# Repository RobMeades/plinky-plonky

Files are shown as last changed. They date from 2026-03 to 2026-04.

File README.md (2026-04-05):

# Introduction
For Christmas 2025 Santa brought Hazel a music box mechanism, henceforth referred to as a "plinky-plonky".  Since it was difficult to turn at speed, I did a quick [motorised version](https://www.youtube.com/watch?v=XHdWuA18UNk) with some bits I was able to get hold of quickly: a motor controller with a speed knob on it and a 5&nbsp;V motor which purported to be silent.  The motor was not silent at all.

Since then I have made a [working Camberwick Green musical box](https://www.meades.org/misc/musical_box/musical_box.html) using one of these mechanisms, employing several varieties of stepper motor and a TMC2209 stepper motor controller.  Hence this repository describes how to make the updated version of the motorised plink-plonky, employing a much quieter stepper motor, TMC2209, ESP32 and using Bluetooth for control.

You can find a video of it in action on [YouTube](https://youtu.be/Unc9a-GsFBE); read on to find out what the lead weights are for.

In order to make this motorised plinky-plonky you will need to be able to:

- 3D print in FDM,
- solder,
- wire-up a small amount of electronics,
- write, or at least compile, C code (based on [ESP-IDF](https://docs.espressif.com/projects/esp-idf/en/stable/esp32/get-started/index.html) for the ESP32),
- write, or at least compile, an Android application to drive the Android Bluetooth API, or download and install the rather spiffy one from the [Releases](https://github.com/RobMeades/plinky-plonky/releases) section of this repo that Google Gemini wrote with a lot of prompting,
- do a tiny amount of woodwork (cutting circular shapes in plywood, sanding, glueing, varnishing).

You will need the following tools:

- an FDM 3D printer,
- a soldering iron,
- a wire stripper, 
- a wire snippers,
- a crimp tool for 0.1&nbsp;inch pitch connectors,
- a set of small allen keys, including 1.5&nbsp;mm and 2.5&nbsp;mm,
- an M3 tap and tap holder,
- a hair drier or other hot air blower capable of shrinking heat-shrink,
- a cross-head screwdriver,
- a largish magnetic flat-head screwdriver,
- an Android phone,
- a coping saw/jigsaw/clever-Dremel-thingy or other means of cutting circular shapes in thin plywood,
- a drill with 3&nbsp;mm and 10&nbsp;mm drill bits,
- fine grade sandpaper,
- a sanding block,
- optional: a very fine modellers paint brush.

# 3D Printed Parts
The 3D printed parts, along with exported `.stl`, are available in the [blender](/blender) folder; see there for printing instructions.

# Parts List
The following parts are required:

- the 3D printed parts from the [blender](blender) folder (which will require filament of your choice),
- a 15&nbsp;note plinky-plonky mechanism with fixing screws: the 3D printed parts are designed for one of [these](https://www.ebay.co.uk/itm/397247369927),
- an ESP32 board with headers soldered-in on the component side: the 3D printed parts are designed for one of [these](https://www.aliexpress.com/item/1005005780805655.html), you could of course modify them to take any small ESP32 board,
- a BigTreeTech TMC2209 board, i.e. one of [these](https://www.aliexpress.com/item/33028050145.html), any "sticky out" pins on the reverse lopped off and heatsink fitted,
- a 12/24&nbsp;V&nbsp;DC to 5&nbsp;V&nbsp;DC regulator: the 3D printed parts are designed for one of [these](https://www.aliexpress.com/item/1005010692851197.html), you could of course modify them to take any small regulator board; the current requirements for the 5&nbsp;V supply are negligible,
- a NEMA17 stepper motor: the 3D printed parts are designed for one of [these](https://www.amazon.co.uk/dp/B0D7PBB17L), frame size 42&nbsp;mm&nbsp;x&nbsp;42&nbsp;mm with M3 threaded mounting holes, frame 20&nbsp;mm deep, shaft 5&nbsp;mm diameter and 20&nbsp;mm long, with flat,
- an AC mains plug-top power supply capable of delivering up to 2&nbsp;Amps at between 12&nbsp;and&nbsp;24&nbsp;V&nbsp;DC, terminating in a 5.5&nbsp;mm diameter barrel connector with a 2.1&nbsp;mm diameter pin, centre-positive,
- an M3 hex-head grub screw (any length, the longer the better),
- 2 off M3&nbsp;x&nbsp;5&nbsp;mm hex head bolts,
- 3 off M3&nbsp;x&nbsp;10&nbsp;mm hex head bolts,
- 4 off M3&nbsp;x&nbsp;5&nbsp;mm pan head bolts,
- 3 off M3&nbsp;x&nbsp;10&nbsp;mm to 15&nbsp;mm pan head bolts,
- a panel-mount DC power socket with 2.1&nbsp;mm diameter pin, 5.5&nbsp;mm diameter barrel outer,
- 1 off 1&nbsp;kOhm resistor,
- a small amount of 7-strand wire in  a few shades of red/orange if you can (input DC Voltage, 5&nbsp;V and 3.3&nbsp;V), black and a signal colour of your choice (e.g. yellow or white or blue),
- a small amount (e.g. 100&nbsp;mm) of 3&nbsp;mm diameter heat-shrink,
- a small amount of flux-cored solder,
- 0.1&nbsp;inch pitch housings (1-way, 2-way and 4-way) plus female pins to go with,
- 2 off pieces (e.g. 10&nbsp;mm square) of double-sided sticky pad, tape or individual pads,
- a small amount (e.g. 400&nbsp;x&nbsp;250&nbsp;mm) of thin (e.g. 3&nbsp;mm thick) plywood,
- a small amount of wide (e.g. 30&nbsp;mm wide) edging that matches the plywood,
- optional: 1 off 4&nbsp;x&nbsp;8&nbsp;x&nbsp;3&nbsp;mm (inside diameter x outside diameter x thickness) bearing: I found that the sheath on the handle of the plinky-plonky mechanism rattled irritatingly so I took it off and slotted the handle into one of these bearings in the 3D printed wheel instead,
- PVA glue,
- possibly a little cyanoacrylate glue (AKA superglue),
- varnish or paint of your choice,
- a small amount of metallic paint (e.g. Humbrol&nbsp;11),
- optional: stick-on felt pads,
- optional: some 0.5&nbsp;kg lead weights e.g. [these from eBay](https://www.ebay.co.uk/itm/145559704455).

# Assembly Instructions
Assembly goes as follows (see also pictures below):

- if you intend to use the bearing to hold the handle of the plinky-plonky mechanism in the wheel, remove the sheath from the handle of the plinky-plonky mechanism by delving about in the end of it with a screwdriver to release the spring clip and hence the sheath,
- fix the plinky-plonky mechanism into place on top of the 3D printed body using the three fixing screws that were supplied with the mechanism, handle facing the stepper motor mount,
- fix the voltage regulator into place in the 3D printed body using the four M3&nbsp;x&nbsp;5&nbsp;mm pan head bolts, input end nearest the round hole in the side of the 3D printed body,
- I had trouble with resonance and, specifically the ESP32 and TMC2209 boards rattling very slightly, so I stuck a few pieces of sticky pad underneath where they would go to dampen things down a bit,
- clip the ESP32 and TMC2209 boards into their mounting positions in the 3D printed body, the TMC2209 board oriented with its red connector nearest the voltage regulator board, clipping the right hand side of both boards in first (when viewed with the lettering the right way up) in order to minimise the chances of damage; the USB-C connector of the ESP32 board needs to be lined up square with the rectangular hole in the 3D printed body,
- trim the stepper motor wires such that they will reach through the channel at the bottom left of the stepper motor mounting bracket and to the TMC22209 board mounting position in the 3D printed box (probably about 150&nbsp;mm) then terminate the wires in a 4-way 0.1&nbsp;inch pitch connector, order as in the schematic below, checking that the stepper motor you are using follows the same colour convention and adjusting as necessary,
- run an M3 tap through the grub screw hole in the 3D printed wheel,
- if you are using the 3D printed wheel that takes the 4&nbsp;x&nbsp;8&nbsp;x&nbsp;3&nbsp;mm bearing, fit the bearing int othe 3D printed wheel now,
- push the handle of the plinky-plonky mechanism into the offset hole in the 3D printed wheel then, with the grub screw hole and the flat on the stepper motor spindle uppermost, push the stepper motor spindle into the centre of the 3D printed wheel from the other side of its mounting bracket (i.e. so the spindle goes through the large central hole in the motor mounting bracket) and, as you do so, pass the stepper motor wires through the hole in the bottom left of the bracket and into the area of the 3D printed body where the boards will be mounted,
- fix the stepper motor to the mounting bracket with the two M3&nbsp;x&nbsp;5&nbsp;mm hex head bolts,
- screw the grub screw into the 3D printed wheel against the flat of the stepper motor spindle, making sure that there is a gap between the wheel and the stepper motor mounting bracket as you tighten the grub screw,
- using some 7-strand signal wire and heat-shrink as appropriate, make a short "Y" assembly with the 1&nbsp;kOhm resistor in series with one of the legs of the Y, all legs terminated in single 0.1&nbsp;inch pitch connectors (see picture below),
- using this, the remaining 7-strand wire and the 0.1&nbsp;inch pitch connectors, wire up the ESP32 board, the TMC2209 board and the stepper motor according to the schematic below, bringing 5&nbsp;V from the output of the voltage regulator and 12&nbsp;to&nbsp;24&nbsp;V from the input of the voltage regulator (you may chose different IO pins on the ESP32 board if you wish, these will be set later when the software for the ESP32 is compiled, though note that pin&nbsp;8 is not used since there is a blue LED on the board connected to this pin and pin&nbsp;20 is not used as it is internally connected to the RF inside the chip),
- wire the panel-mount power socket to the input of the voltage regulator board, with the central pin of the panel mount socket to the positive, adding heat-shrink to cover any exposed connector (since there is little room in the box),
- fit the panel-mount power socket into its mounting hole in the 3D printed body,
- plug an AC mains 12&nbsp;/nbsp;24&nbsp;V DC plug-top power supply into the power socket and you should see a red light on the ESP32 board,
- fix the 3D printed stepper motor cover to the stepper motor mounting bracket with two of the M3&nbsp;x&nbsp;10&nbsp;mm hex head bolts,
- fix the 3D printed lid into position over the electronics with the remaining M3&nbsp;x&nbsp;10&nbsp;mm hex head bolt,
- proceed to "Bring Up" below.

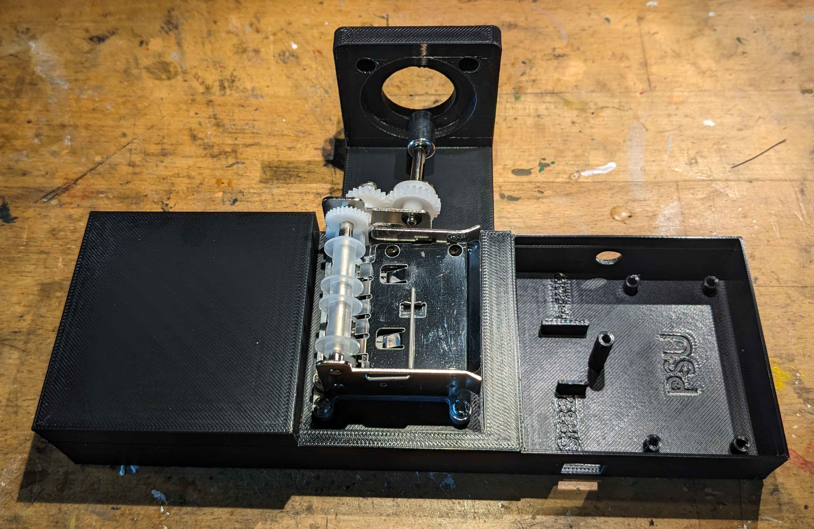
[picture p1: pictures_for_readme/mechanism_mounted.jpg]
Mechanism mounted
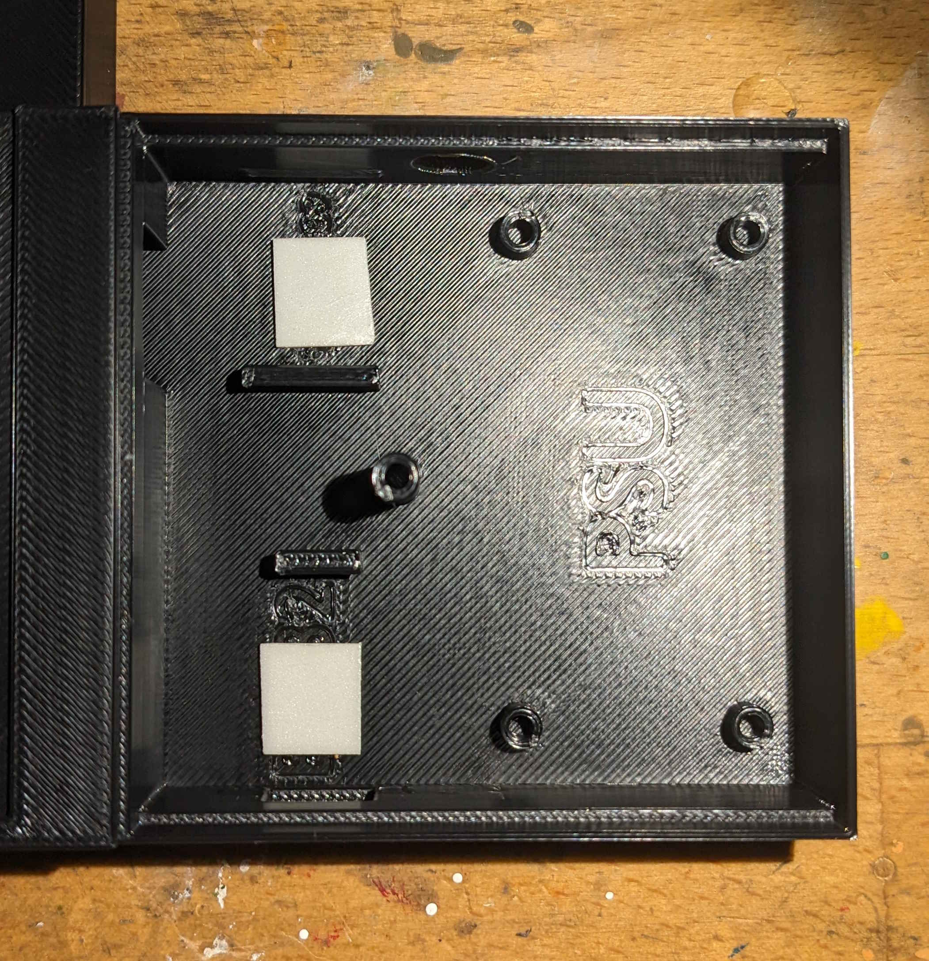
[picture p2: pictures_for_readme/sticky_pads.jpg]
Sticky pads
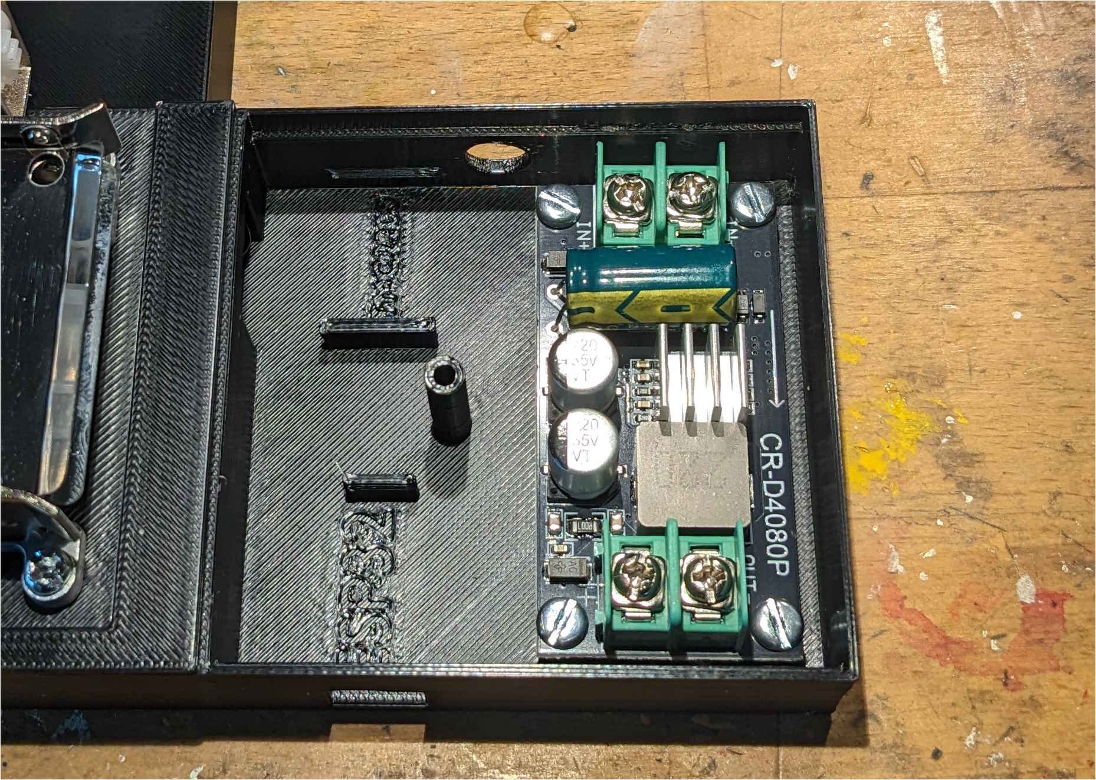
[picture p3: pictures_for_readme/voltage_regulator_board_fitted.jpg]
Voltage regulator board fitted
  

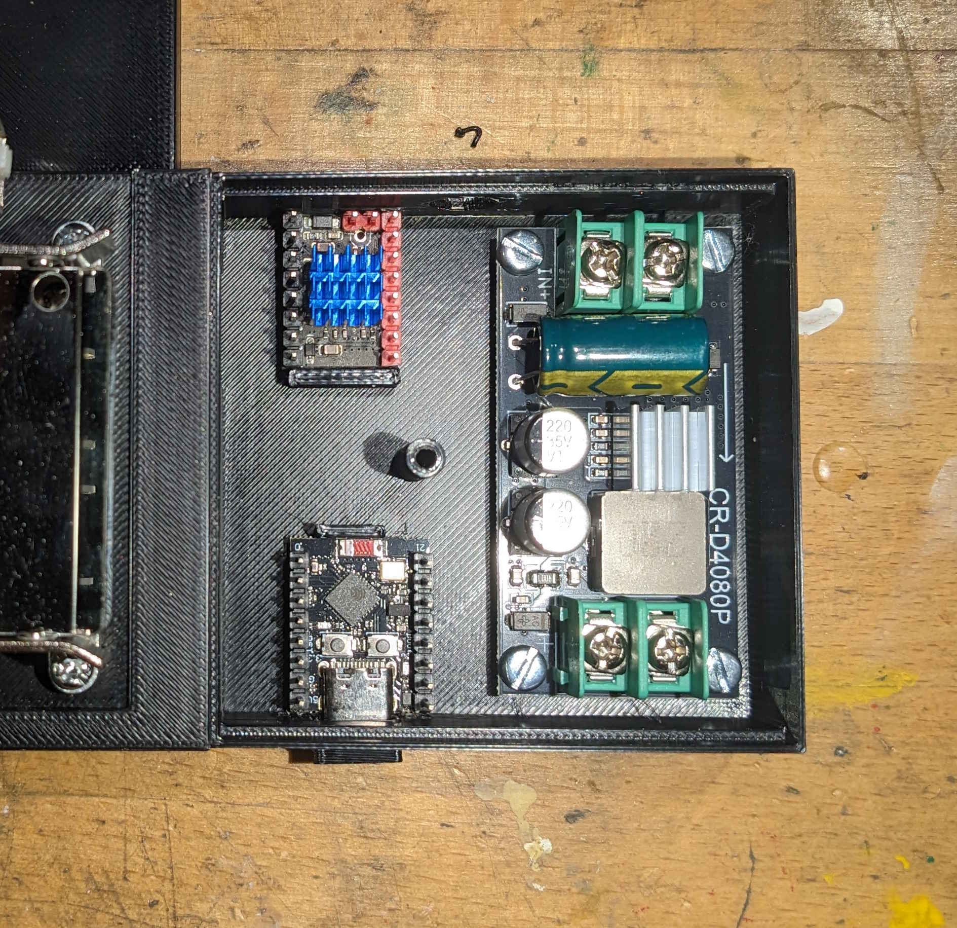
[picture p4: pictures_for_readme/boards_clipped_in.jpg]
Boards clipped in
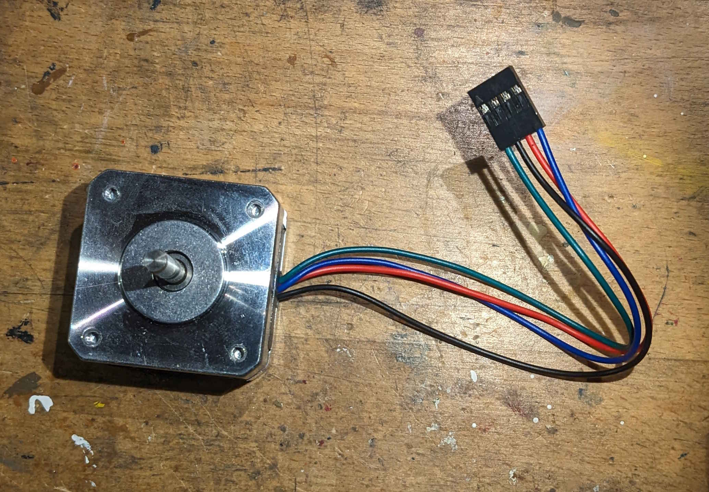
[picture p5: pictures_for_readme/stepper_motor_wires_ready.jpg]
Stepper motor wires trimmed and connector fitted
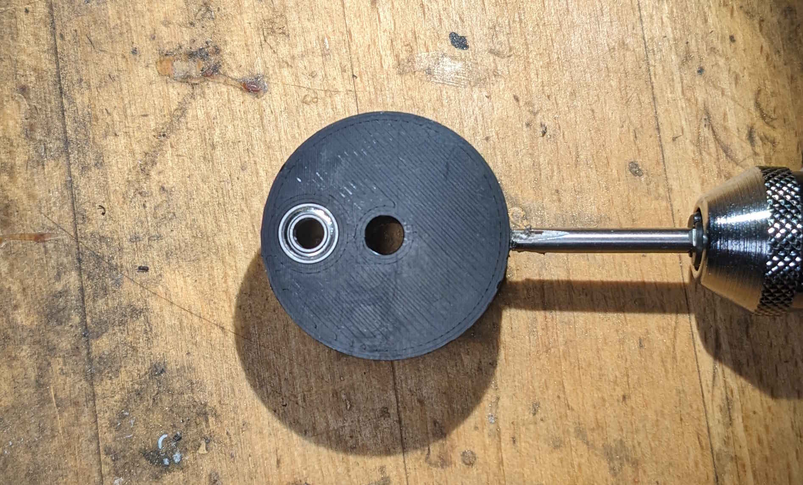
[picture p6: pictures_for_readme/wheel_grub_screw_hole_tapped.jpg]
Wheel grub screw hole tapped
  

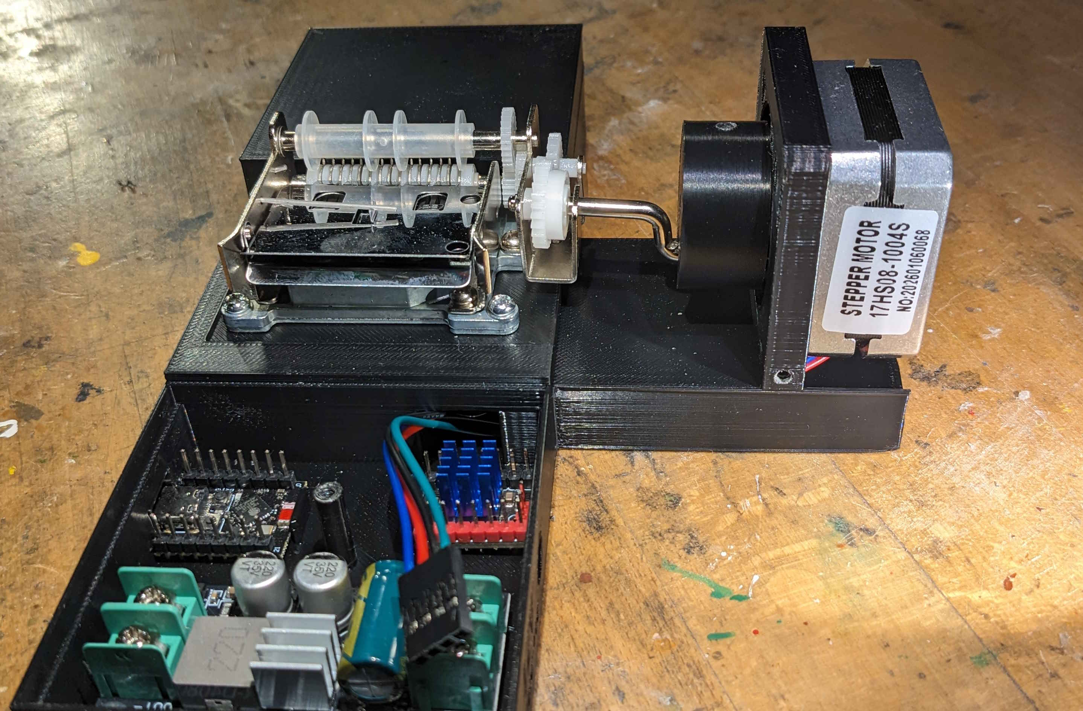
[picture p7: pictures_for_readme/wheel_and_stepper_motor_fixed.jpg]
Wheel and stepper motor fixed
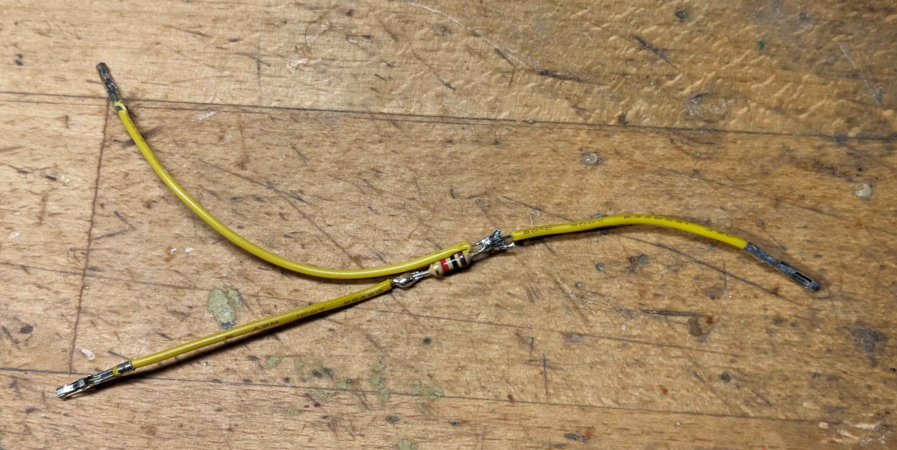
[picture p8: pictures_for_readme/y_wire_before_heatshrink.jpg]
Y-wire before heatshrink
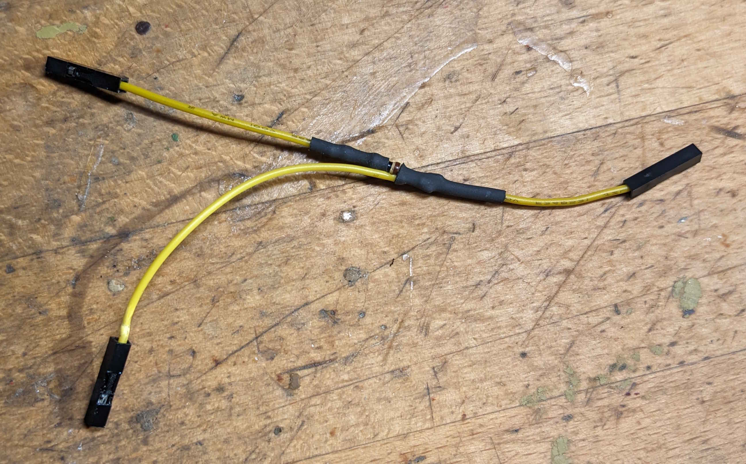
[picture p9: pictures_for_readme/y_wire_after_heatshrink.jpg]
Y-wire after heatshrink
  

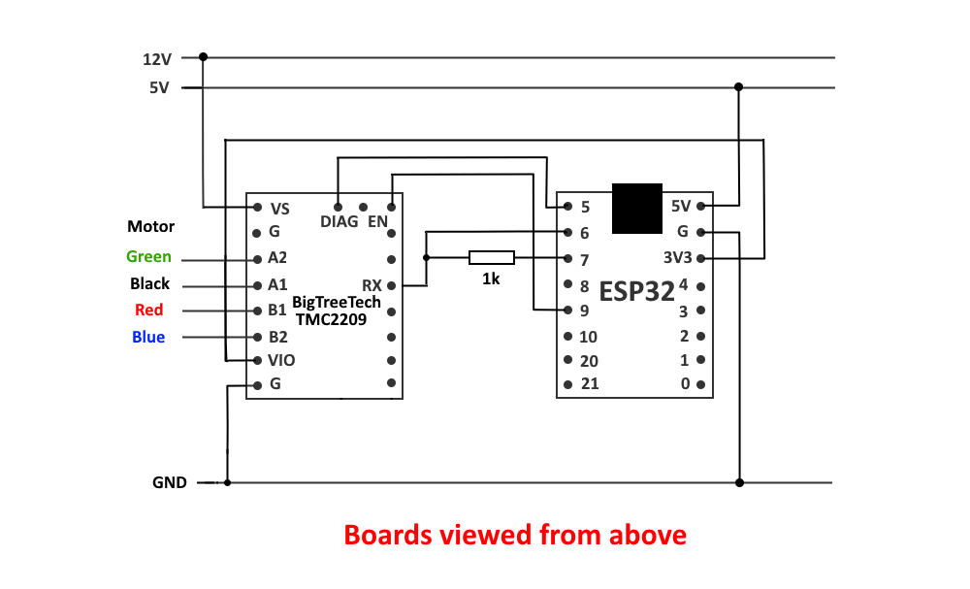
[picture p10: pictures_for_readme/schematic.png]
Schematic


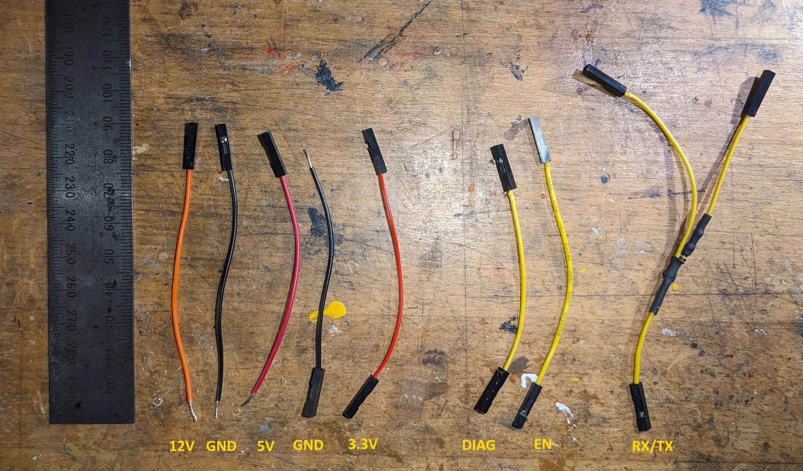
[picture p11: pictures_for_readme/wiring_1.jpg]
Wires cut to length and connectors fitted
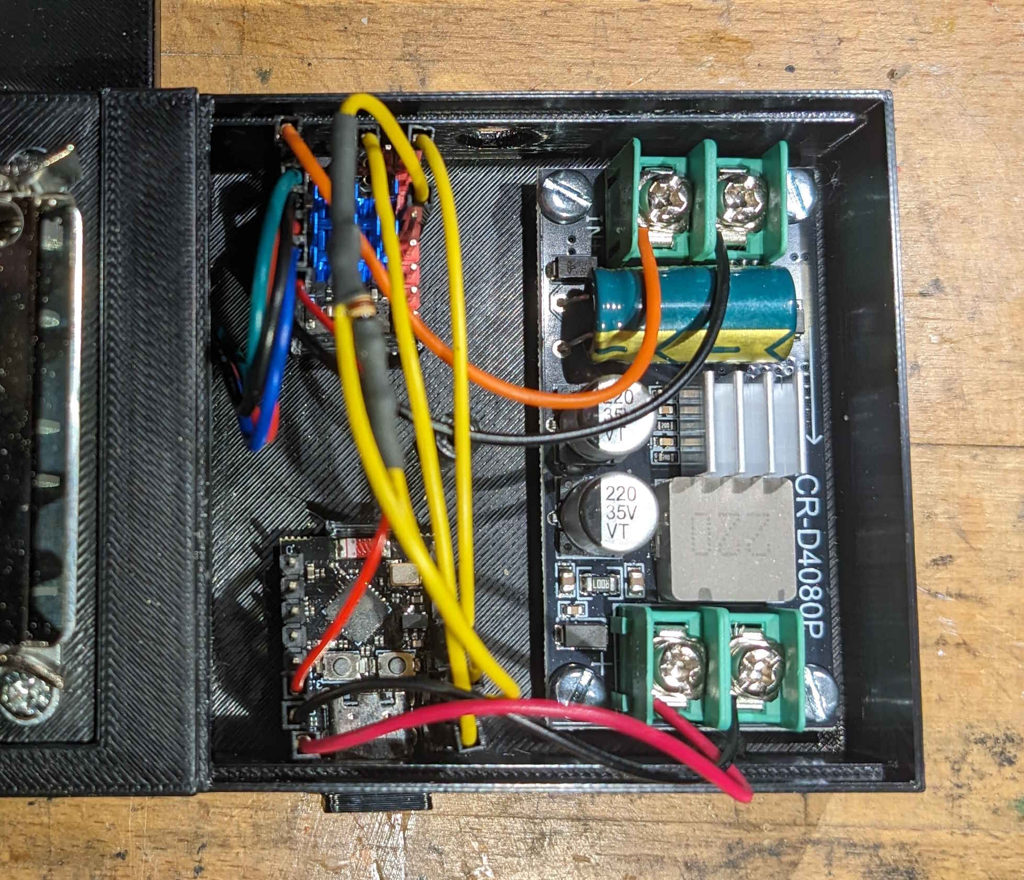
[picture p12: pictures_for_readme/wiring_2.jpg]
Wiring completed
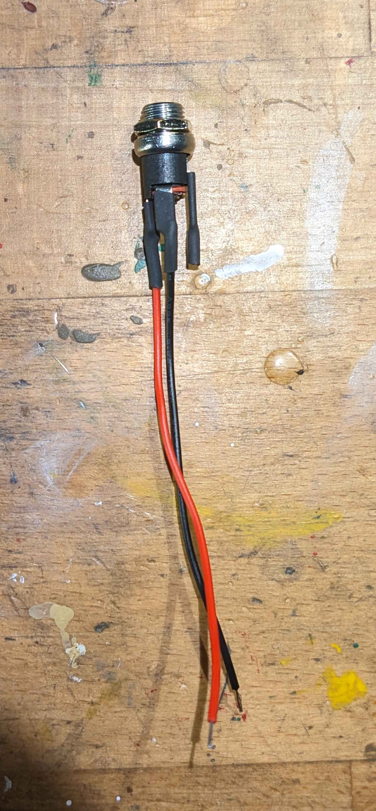
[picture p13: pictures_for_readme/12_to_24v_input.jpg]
power socket with wires attached and heat-shrinked
  

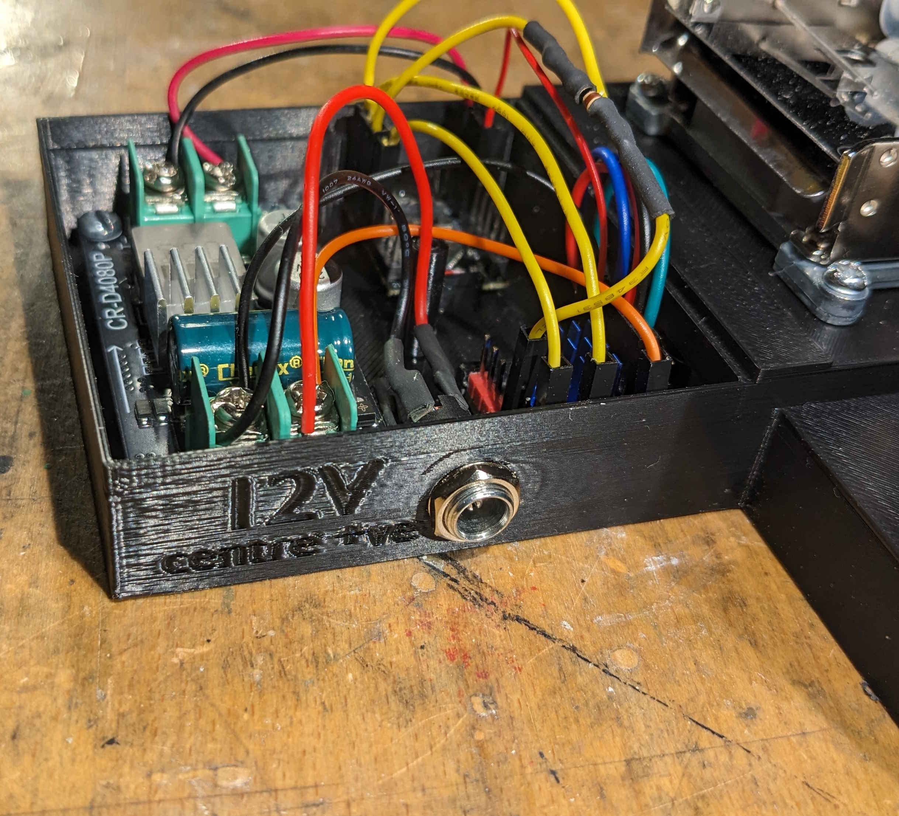
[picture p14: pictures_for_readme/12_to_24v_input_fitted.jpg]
power socket fitted
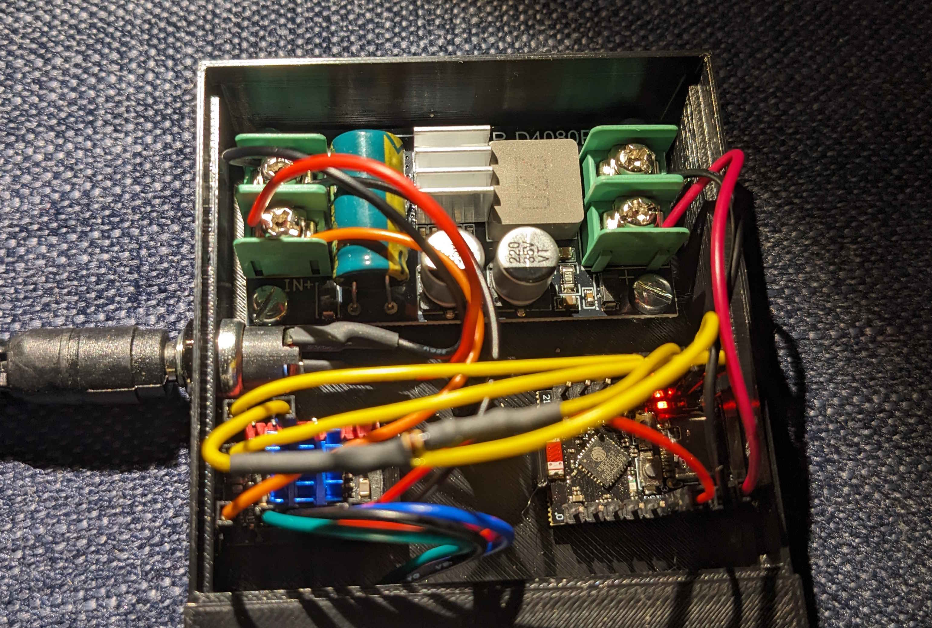
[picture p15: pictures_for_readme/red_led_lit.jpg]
power plugged in, LED lit
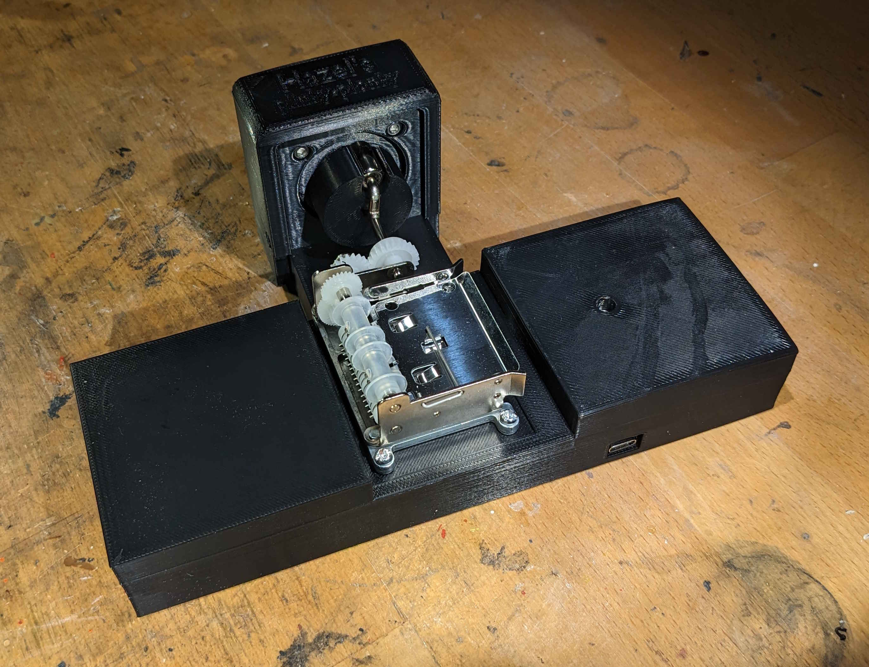
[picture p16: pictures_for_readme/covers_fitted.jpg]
Covers fitted
  

# Bring Up
Bring up goes as follows:

- plug a PC on which the [ESP-IDF software environment](https://docs.espressif.com/projects/esp-idf/en/stable/esp32/get-started/index.html) has been installed into the USB socket of the ESP32 board: a USB device should appear on the PC (e.g. `/dev/ttyACM0` on Linux); there is no need to plug external power into the plinky-plonky just yet as it should be able to draw sufficient power for these initial tests from the USB,
- build the software that is contained in the [software/esp32](/software/esp32) directory and download it to the ESP32 via USB; if you have wired up different GPIO pins on the ESP32 to those in the schematic above, change the values in [Kconfig.projbuild](/software/esp32/main/Kconfig.projbuild) before compiling,
- when the code runs on the ESP32 nothing much should happen, you will need an Android application for that, but if you see a splurge of "STALL" in the logged output of the ESP32 then you _do_ need to supply external power to the plinky-plonky,
- either install the pre-built Android `.apk` from the [Releases](https://github.com/RobMeades/plinky-plonky/releases) section of this repository on an Android phone or, if you wish to build/modify the application yourself, follow the instructions in the [software/android](/software/android) directory; Android will show a `Play Protect` warning, which is normal for an independent, open-source project: to install tap `More Details` and then `Install Anyway`,
- make sure you have Bluetooth enabled on the Android phone, hold the phone upright (portait orientation) and launch the application,
- give the application the permissions it asks for (required to access Bluetooth) and, with the plinky-plonky powered-up, use the application to scan for and connect to the plinky-plonky; if the Android phone fails to find the plinky-plonky, try disabling and then re-enabling Bluetooth on the phone and trying again (Android Bluetooth is a mess),
- press `Play` to have the motor run, `Stop` to stop it, adjust the speed using the knob or turn the phone landscape for the ability to generate complicated speed patterns,
- if you find that the plinky-plonky rattles at certain speeds, even when you have used the bearing approach, that will likely be because the handle can be slightly loose in the bearing: should that be the case, drop a _very_ tiny amount of cyanoacrylate glue between the handle and the inner face of the bearing to stop it rattling around, being _extremely_ careful not to get any glue on the runners of the bearing as you do so,
- rattles/resonance can also be removed by going around and gently tighting the fixing bolts,
- if that fails, since resonances can be in different components at different frequencies, I purchased some lead weights and kept three to hand for placing on whatever bit of the plinky-plonky needed damping at that running frequency (obviously wash your hands after handling lead),
- when you are satisfied that the plinky-plonky runs sweetly, push the 3D printed USB cover into the rectangular hole in the 3D printed body to prevent anything getting into the USB connector and proceed to "Finishing Off" below.

# Finishing Off
In order to give the plinky-plonky a solid yet resonant (in a good way) base:

- cut two pieces of thin plywood to the shape of the 3D printed `base_outer` (see pictures below),
- into one of these pieces drill three 3&nbsp;mm diameter holes to match the positions of the holes in the bottom of the 3D printed body, orienting that body nicely,
- into the other piece drill three rather wider (e.g. 10&nbsp;mm diameter) access holes in the same locations,
- glue the two pieces of plywood, in the same orientation, either side of `base_outer` with PVA, to make a kind of giant Oreo cookie, ensuring that the holes and the access holes align,
- glue an edging strip that matches the colour of the plywood around `base_outer` with PVA,
- when the glue has set, rub the whole thing down with fine sandpaper,
- varnish/finish in whatever way pleases you,
- to make the next step easier, create the threads in each of the holes in the bottom of the 3D printed body using one of the longer M3 pan head bolts,
- using the access holes to get at the 3&nbsp;mm diameter holes, attach the wooden/plastic base to the bottom of the 3D printed body with the longer M3 pan head bolts; a magnetic flat-head screwdriver is your friend,
- if you find that the plink-plonky resonates somewhat when running placed on a hard surface, stick-on felt pads or rubber feet help.

Finally, pick out the lettering embossed into the 3D printed stepper motor cover in metallic paint using a very fine modeller's paint brush.

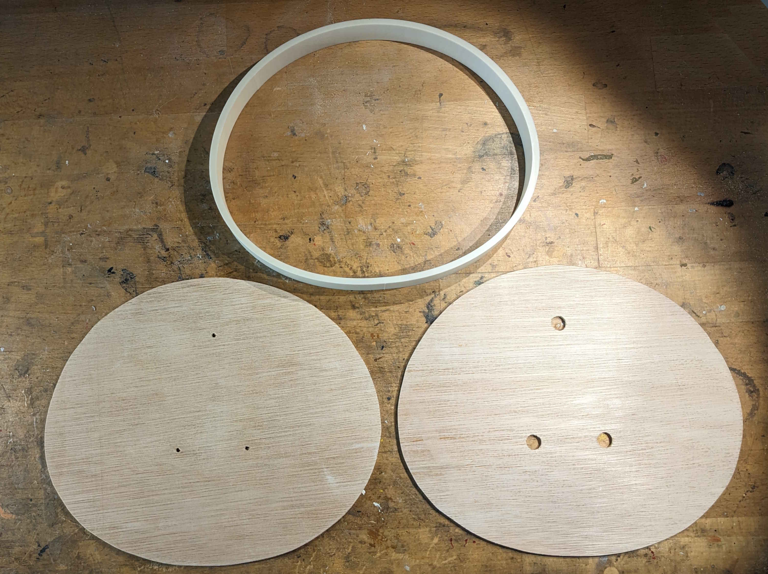
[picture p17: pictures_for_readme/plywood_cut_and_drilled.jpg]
Plywood cut and drilled
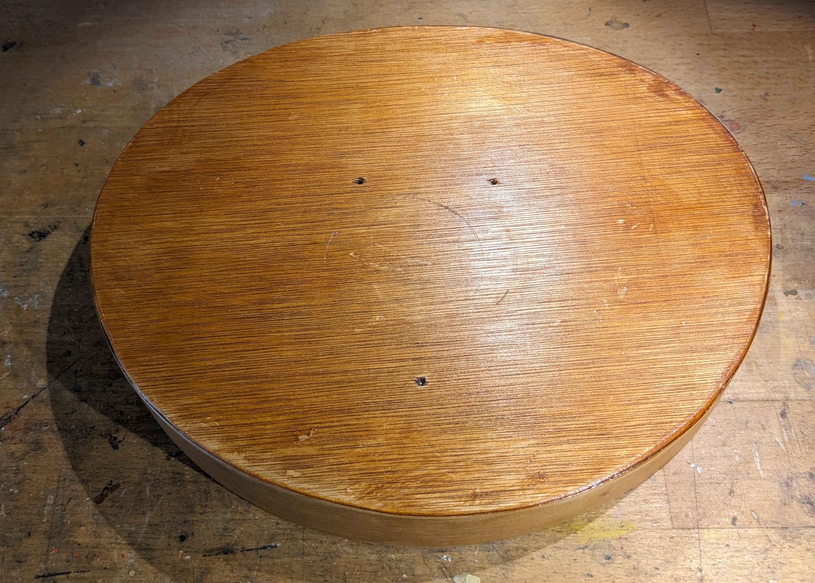
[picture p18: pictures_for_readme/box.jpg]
Box, varnished
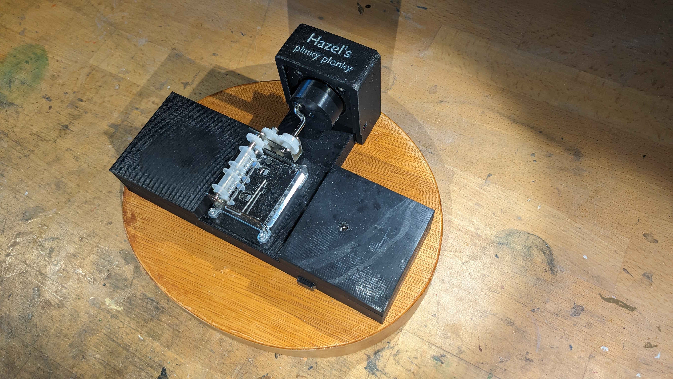
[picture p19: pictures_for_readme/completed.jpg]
Completed


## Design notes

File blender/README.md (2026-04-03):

# Introduction
This folder contains the 3D printed parts.  I printed all of the parts in ASA for longevity but any material will do.

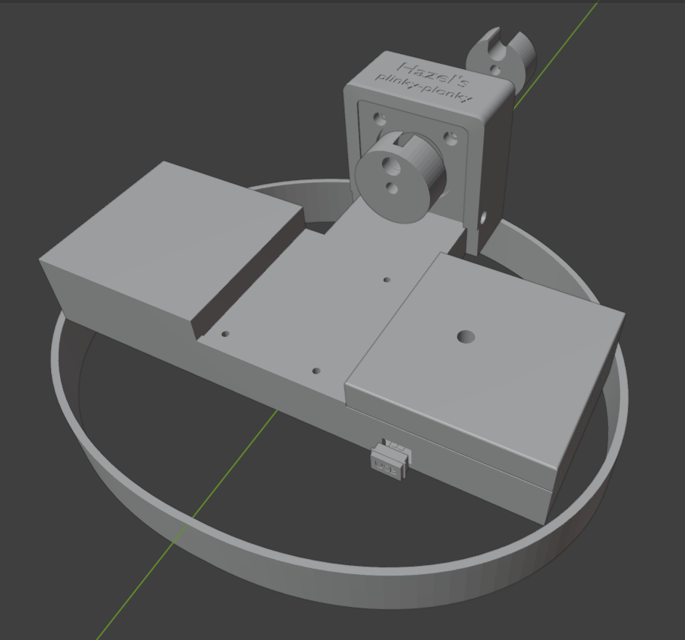
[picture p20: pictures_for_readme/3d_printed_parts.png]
Blender


# Printing Instructions
All parts should be printed at fastest speed, 15% in-fill, probably in black, aside from `base_outer` which you may wish to print in natural ASA, a better colour match for the plywood that it will be sandwiched between.  No supports should be required for any part except for the lid, which will need supports on the build plate for the screw hole.

You have a choice where the wheel is concerned: print either `wheel_for_unmodified_handle` or `wheel_for_handle_no_sheath`.  I found that the sheath on the handle of the plinky-plonky mechanism, designed to make operating it by hand easier, wrattled irritatingly and so I took the sheath off and printed `wheel_for_handle_no_sheath` into which I fitted a 4&nbsp;x&nbsp;8&nbsp;x&nbsp;3&nbsp;mm bearing to take the inner part of the handle.  If you prefer not to remove the sheath, print `wheel_for_unmodified_handle` instead.

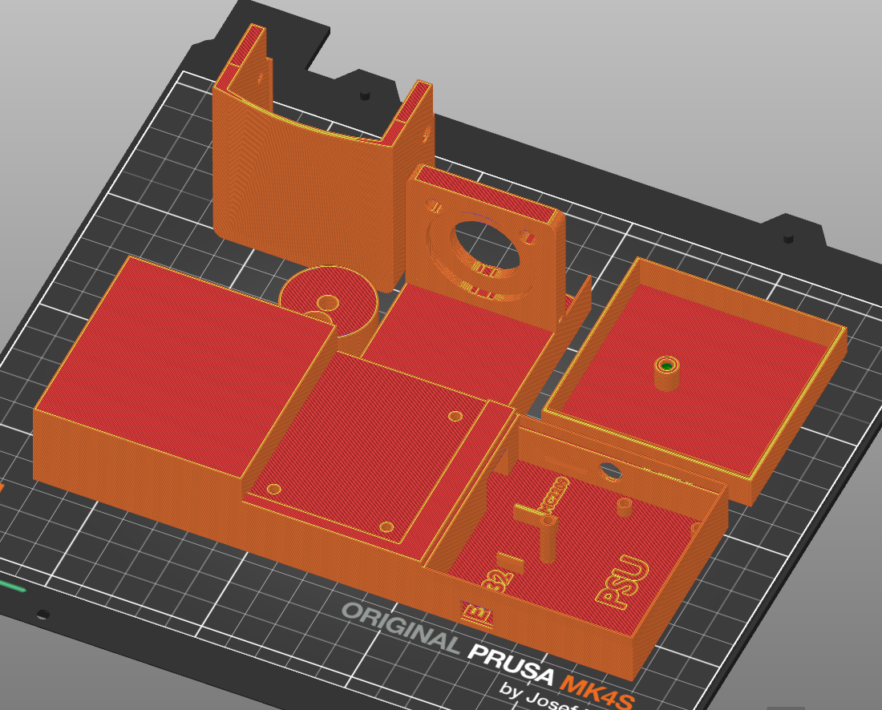
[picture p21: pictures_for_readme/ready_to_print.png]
Main parts ready to print
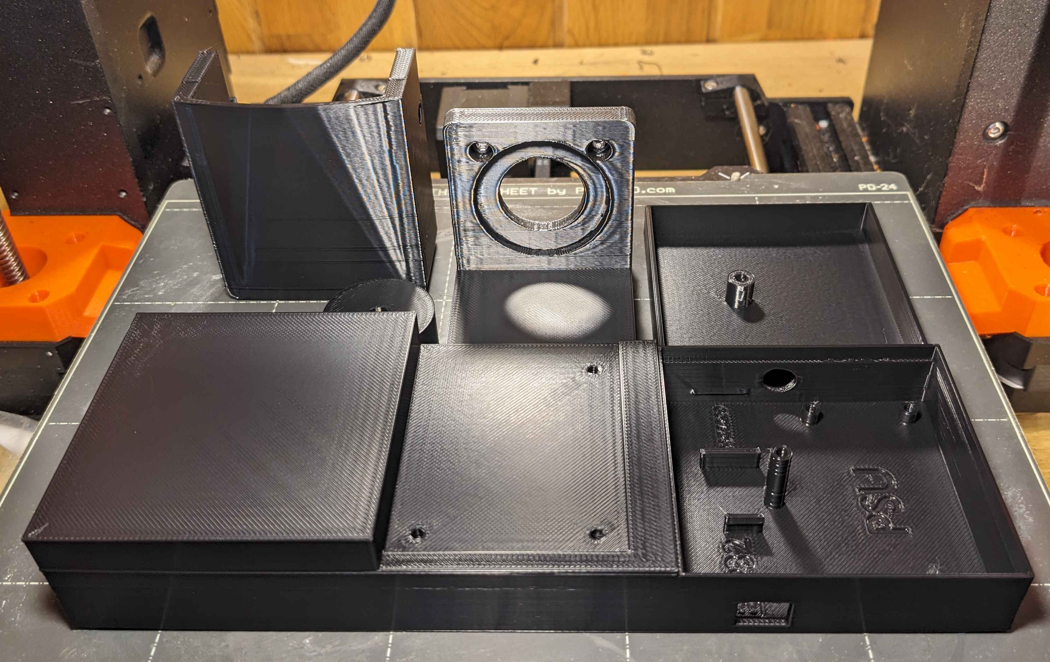
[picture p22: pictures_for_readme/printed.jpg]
Main parts printed
 

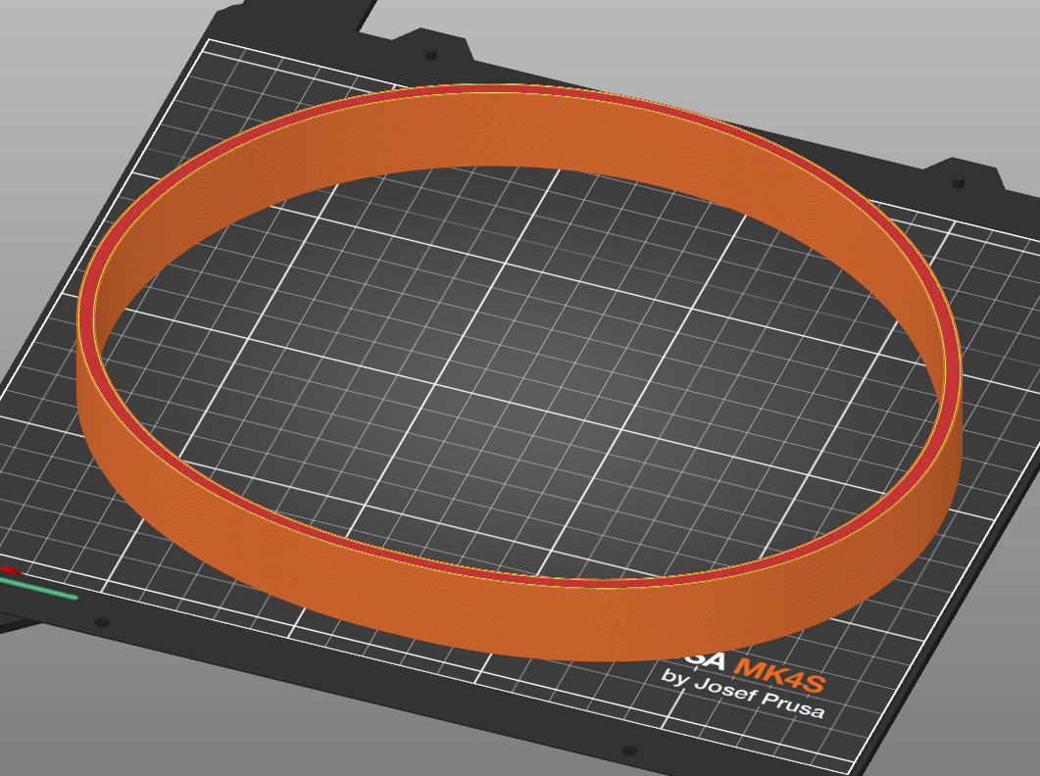
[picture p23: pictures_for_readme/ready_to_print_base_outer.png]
Base outer ready to print
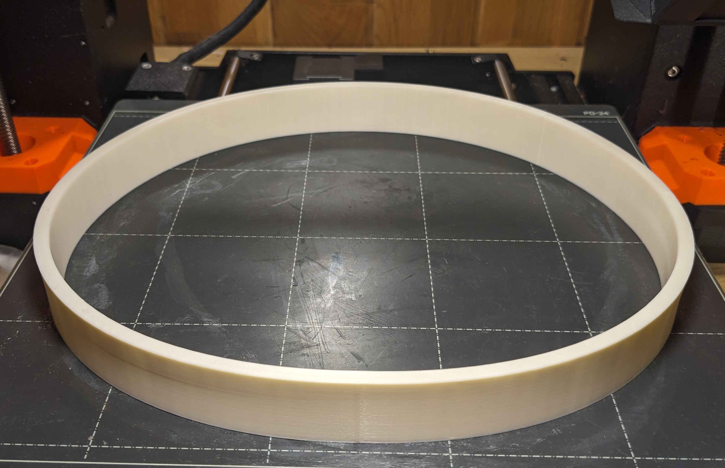
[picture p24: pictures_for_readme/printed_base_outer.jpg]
Base outer printed


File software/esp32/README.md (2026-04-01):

# Introduction
This folder contains the software for the ESP32-side of the plinky-plonky.

On a PC set up with the [ESP-IDF](https://docs.espressif.com/projects/esp-idf/en/stable/esp32/get-started/index.html) software environment, compile this software with the default values and download it to the ESP32 in the plinky-plonky using a USB cable.  If you have chosen to wire up different GPIO pins on the ESP32 to the ones given in the [schematic](/pictures_for_readme/schematic.png) on the main page, change those values in [Kconfig.projbuild](main/Kconfig.projbuild) before compiling.

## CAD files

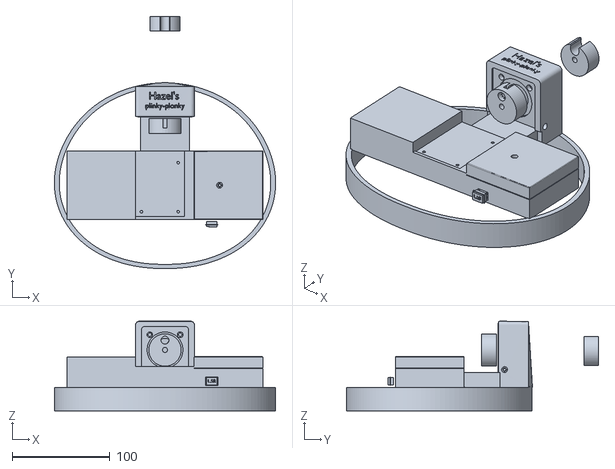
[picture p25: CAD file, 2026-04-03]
blender/plinky_plonky.stl
225.8 x 257.2 x 91.5

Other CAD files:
blender/plinky_plonky.blend

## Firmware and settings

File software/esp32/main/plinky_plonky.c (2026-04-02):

/*
 * Copyright 2026 Rob Meades
 *
 * Licensed under the Apache License, Version 2.0 (the "License");
 * you may not use this file except in compliance with the License.
 * You may obtain a copy of the License at
 *
 * http://www.apache.org/licenses/LICENSE-2.0
 *
 * Unless required by applicable law or agreed to in writing, software
 * distributed under the License is distributed on an "AS IS" BASIS,
 * WITHOUT WARRANTIES OR CONDITIONS OF ANY KIND, either express or implied.
 * See the License for the specific language governing permissions and
 * limitations under the License.
 */

/** @file
 * @brief Implementation of a steppper-motor driven plinky-plonky.
 */

#include <string.h>
#include <inttypes.h>
#include "freertos/FreeRTOS.h"
#include "freertos/task.h"
#include "freertos/queue.h"
#include "esp_event.h"
#include "esp_log.h"
#include "errno.h"
#include "driver/uart.h"
#include "driver/gpio.h"
#include "esp_timer.h"
#include "esp_task_wdt.h"
#include "nvs.h"
#include "nvs_flash.h"
#include "esp_bt.h"
#include "nimble/nimble_port.h"
#include "nimble/nimble_port_freertos.h"
#include "host/ble_hs.h"
#include "services/gap/ble_svc_gap.h"
#include "services/gatt/ble_svc_gatt.h"
#include "host/ble_gap.h"
#include "host/ble_hs.h"
#include "host/ble_store.h"
#include "host/ble_sm.h"      // For security manager constants
#include "host/util/util.h"

#include "tmc2209.h"

/* ----------------------------------------------------------------
 * COMPILE-TIME MACROS
 * -------------------------------------------------------------- */

 // Logging prefix
 #define TAG "plinky-plonky"

// UART buffer
#define UART_RX_BUFFFER_SIZE 256

// The addresss of the TMC2209 device we are going to us
#define TMC2209_ADDRESS 0

// The number of milliseconds to vTaskDelay() for in order to let the idle task
// to feed its watchdog
 #define WATCHDOG_FEED_TIME_MS 10

// The sense resisitor wired to the BRA and BRB pins of the TMC2209,
// the BigTreeTech board uses 100 milliOhms
#define TMC2209_RSENSE_MOHM 110

// Standard short duration for an LED lash
#define DEBUG_LED_SHORT_MS 50

// Standard short duration for a long LED lash
#define DEBUG_LED_LONG_MS 1000

// The motor current to set, in milliAmps
#define STEPPER_MOTOR_ACTIVE_CURRENT_MA 1000

// The percentage of the run current to apply during hold;
// don't need a lot, let it cool down
#define STEPPER_MOTOR_HOLD_CURRENT_PERCENT 20

// The microstep resolution to employ
#define STEPPER_MOTOR_MICROSTEP_RESOLUTION 256

// The default stepper motor velocity
#define STEPPER_MOTOR_DEFAULT_VELOCITY_MILLIHERTZ (64 * 7 * STEPPER_MOTOR_MICROSTEP_RESOLUTION)

// The maximum speed change step to do it one go
#define STEPPER_MOTOR_SPEED_MILLIHERTZ_CHANGE_MAX 1000000

// The speed change step when starting
#define STEPPER_MOTOR_SPEED_MILLIHERTZ_START_MAX 10

// The interval between speed changes if they have to
// be done in more than one step
#define STEPPER_MOTOR_SPEED_MILLIHERTZ_CHANGE_INTERVAL_MS 0

// The name that we appear under in Bluetooth
#define BLE_DEVICE_NAME "Plinky-Plonky"

// Service UUID for plinky-plonky control
#define PLINKY_PLONKY_SERVICE_UUID            0xFFE0

// Characteristic UUID for "play" command (Boolean)
#define PLINKY_PLONKY_PLAY_UUID               0xFFE1

// Characteristic UUID for "speed" command (uint32_t)
#define PLINKY_PLONKY_SPEED_MILLIHERTZ_UUID   0xFFE2

// The name for the speed entry in non-volatile storage.
#define NVS_NAME_SPEED "speed"

/* ----------------------------------------------------------------
 * TYPES
 * -------------------------------------------------------------- */

// The context for the plinky-plonky.
typedef struct {
    TaskHandle_t stall_task_handle;
    SemaphoreHandle_t diag_semaphore;
    QueueHandle_t ble_command_queue;
    TaskHandle_t ble_command_task_handle;
    ble_uuid16_t plinky_plonky_service_uuid;
    struct ble_hs_adv_fields ble_adv_fields;
    uint16_t ble_connection_handle;
    bool running;
    bool play_not_stop;
    uint32_t speed_milliHertz;
} plinky_plonky_context_t;

// Plinky-plonky commands.
typedef enum {
    COMMAND_NONE,
    COMMAND_UNKNOWN,
    COMMAND_WRITE_PLAY,
    COMMAND_WRITE_SPEED_MILLIHERTZ,
    COMMAND_READ_PLAY,
    COMMAND_READ_SPEED_MILLIHERTZ
} command_type_t;

// Command queue contents.
typedef struct {
    uint16_t uuid;
    command_type_t type;
    uint32_t value;
} command_t;

/* ----------------------------------------------------------------
 * VARIABLES (THERE ARE MORE FURTHER DOWN)
 * -------------------------------------------------------------- */

// Set up valid advertising parameters.
static const struct ble_gap_adv_params g_ble_adv_params = {
    .conn_mode = BLE_GAP_CONN_MODE_UND,   // Connectable undirected advertising
    .disc_mode = BLE_GAP_DISC_MODE_GEN,   // General discoverable mode
    // Values are in 0.625ms units
    // 160 = 100ms, 320 = 200ms
    .itvl_min = 160,                      // Minimum advertising interval (100 ms)
    .itvl_max = 320};                     // Maximum advertising interval (200 ms)

// Context for the whole application
static plinky_plonky_context_t g_plinky_plonky_context = {
    .stall_task_handle = NULL,
    .diag_semaphore = NULL,
    .ble_command_queue = NULL,
    .ble_command_task_handle = NULL,
    .plinky_plonky_service_uuid = BLE_UUID16_INIT(PLINKY_PLONKY_SERVICE_UUID),
    .ble_adv_fields = {0},
    .ble_connection_handle = BLE_HS_CONN_HANDLE_NONE,
    .running = true,
    .play_not_stop = false,
    .speed_milliHertz = STEPPER_MOTOR_DEFAULT_VELOCITY_MILLIHERTZ};

// THERE ARE MORE VARIABLE FURTHER DOWN

/* ----------------------------------------------------------------
 * STATIC FUNCTIONS: MISC
 * -------------------------------------------------------------- */

// Flash the debug LED
static void flash_debug_led(int32_t duration_ms)
{
#if defined(CONFIG_PLINKY_PLONKY_DEBUG_LED_PIN) && (CONFIG_PLINKY_PLONKY_DEBUG_LED_PIN >= 0)
    gpio_set_level(CONFIG_PLINKY_PLONKY_DEBUG_LED_PIN, 0);
    vTaskDelay(pdMS_TO_TICKS(duration_ms));
    gpio_set_level(CONFIG_PLINKY_PLONKY_DEBUG_LED_PIN, 1);
#endif
}

/* ----------------------------------------------------------------
 * STATIC FUNCTIONS: NVS RELATED
 * -------------------------------------------------------------- */

// Retrieve the stored speed value from NVS, returns
// ESP_ERR_NVS_NOT_FOUND if the value is not initialised.
static esp_err_t nvs_speed_millihertz_get(uint32_t *speed_milliHertz)
{
    nvs_handle_t nvs_handle;

    esp_err_t err = nvs_open("storage", NVS_READONLY, &nvs_handle);
    if (err == ESP_OK) {
        err = nvs_get_u32(nvs_handle, NVS_NAME_SPEED,
                          speed_milliHertz);
        if (err != ESP_OK) {
            ESP_LOGW(TAG, "Unable read \"%s\" from NVS:"
                     " 0x%04x (\"%s\")!", NVS_NAME_SPEED,
                      err, esp_err_to_name(err));
        }
        nvs_close(nvs_handle);
    } else {
        ESP_LOGE(TAG, "Unable to open NVS for read: 0x%04x (\"%s\")!", err, esp_err_to_name(err));
    }

    return err;
}

// Set the stored speed value in NVS.
static esp_err_t nvs_speed_millihertz_set(uint32_t speed_milliHertz)
{
    nvs_handle_t nvs_handle;

    esp_err_t err = nvs_open("storage", NVS_READWRITE, &nvs_handle);
    if (err == ESP_OK) {
        err = nvs_set_u32(nvs_handle, NVS_NAME_SPEED,
                          speed_milliHertz);
        if (err == ESP_OK) {
            err = nvs_commit(nvs_handle);
            if (err != ESP_OK)  {
                ESP_LOGE(TAG, "Unable to commit changes to NVS:"
                        " 0x%04x (\"%s\")!", err, esp_err_to_name(err));
            }
        } else {
            ESP_LOGE(TAG, "Unable write \"%s\" to NVS:"
                     " 0x%04x (\"%s\")!", NVS_NAME_SPEED,
                     err, esp_err_to_name(err));
        }
        nvs_close(nvs_handle);
    } else {
        ESP_LOGE(TAG, "Unable to open NVS for read/write: 0x%04x (\"%s\")!",
                 err, esp_err_to_name(err));
    }

    return err;
}

/* ----------------------------------------------------------------
 * STATIC FUNCTIONS: STEPPER MOTOR RELATED
 * -------------------------------------------------------------- */

#if defined CONFIG_PLINKY_PLONKY_DIAG_PIN && (CONFIG_PLINKY_PLONKY_DIAG_PIN >= 0)

// DIAG interrupt handler,
static void diag_interrupt_handler(void *handler_arg)
{
    plinky_plonky_context_t *context = (plinky_plonky_context_t *) handler_arg;
    BaseType_t higherPriorityTaskWoken;

    if (context->stall_task_handle && context->diag_semaphore) {
        xSemaphoreGiveFromISR(context->diag_semaphore, &higherPriorityTaskWoken);
        portYIELD_FROM_ISR(higherPriorityTaskWoken);
    }
}

#endif

// Task to handle stall indications.
static void stall_task(void *arg)
{
    plinky_plonky_context_t * context = (plinky_plonky_context_t *) arg;

    while (context->running) {
        xSemaphoreTake(context->diag_semaphore, portMAX_DELAY);
        ESP_LOGI(TAG, "STALL");
    }

    vTaskDelete(NULL);
}

/* ----------------------------------------------------------------
 * STATIC FUNCTION PROTOTYPE: NEEDED FOR BLE CALLBACKS
 * -------------------------------------------------------------- */

static int ble_gap_event_callback(struct ble_gap_event *event, void *arg);

/* ----------------------------------------------------------------
 * STATIC FUNCTIONS: BLE
 * -------------------------------------------------------------- */

// Change speed gradually.
static int32_t velocity_change(int32_t target_speed_millihertz)
{
    int32_t err = 0;
    int32_t target_velocity = target_speed_millihertz * STEPPER_MOTOR_MICROSTEP_RESOLUTION;
    int32_t velocity_step = STEPPER_MOTOR_SPEED_MILLIHERTZ_CHANGE_MAX * STEPPER_MOTOR_MICROSTEP_RESOLUTION;

    int32_t velocity = 0;
    tmc2209_get_velocity(TMC2209_ADDRESS, &velocity);
    if (target_velocity < velocity) {
        velocity_step = -velocity_step;
    }
    while ((velocity != target_velocity) && (err >= 0)) {
        velocity += velocity_step;
        if (velocity_step > 0) {
            if (velocity > target_velocity) {
                velocity = target_velocity;
            }
        } else {
            if (velocity < target_velocity) {
                velocity = target_velocity;
            }
        }
        err = tmc2209_set_velocity(TMC2209_ADDRESS, velocity);
        ESP_LOGI(TAG, "BLE tmc2209_set_velocity for velocity %d returned %d.", velocity, err);
        if ((err >= 0) && (velocity != target_velocity)) {
            vTaskDelay(pdMS_TO_TICKS(STEPPER_MOTOR_SPEED_MILLIHERTZ_CHANGE_INTERVAL_MS));
        }
    }

    return err;
}

// Task to handle BLE commands.
static void ble_command_task(void *arg)
{
    plinky_plonky_context_t * context = (plinky_plonky_context_t *) arg;
    command_t command;
    int32_t err = 0;
    int32_t velocity = 0;

    while (context->running) {
        if (xQueueReceive(context->ble_command_queue, &command, pdMS_TO_TICKS(100))) {
            switch (command.type) {
                case COMMAND_WRITE_PLAY:
                    context->play_not_stop = command.value;
                    // When stopping and starting we also change
                    // the velocity (gradually in the case of starting
                    // up), otherwise the motor can make a bit of a "clunk"
                    // noise
                    if (context->play_not_stop) {
                        tmc2209_motor_enable(TMC2209_ADDRESS);
                        err = velocity_change(context->speed_milliHertz);
                        if (err < 0) {
                            velocity = 0;
                            tmc2209_get_velocity(TMC2209_ADDRESS, &velocity);
                            ESP_LOGE(TAG, "BLE unable to set speed to %lu milliHertz at start (%d), speed"
                                    " is now %d milliHertz!", context->speed_milliHertz, err,
                                    velocity / STEPPER_MOTOR_MICROSTEP_RESOLUTION);
                            context->speed_milliHertz = velocity / STEPPER_MOTOR_MICROSTEP_RESOLUTION;
                        }
                    } else {
                        tmc2209_motor_disable(TMC2209_ADDRESS);
                        tmc2209_set_velocity(TMC2209_ADDRESS, 0);
                    }
                    ESP_LOGI(TAG, "BLE command (0x%04x), write: %s.",
                             command.uuid, context->play_not_stop ? "play" : "stop");
                    break;
                case COMMAND_WRITE_SPEED_MILLIHERTZ:
                    err = velocity_change((int32_t) command.value);
                    velocity = 0;
                    tmc2209_get_velocity(TMC2209_ADDRESS, &velocity);
                    context->speed_milliHertz = velocity / STEPPER_MOTOR_MICROSTEP_RESOLUTION;
                    if (err >= 0) {
                        ESP_LOGI(TAG, "BLE speed set to %lu milliHertz.", context->speed_milliHertz);
                        nvs_speed_millihertz_set(context->speed_milliHertz);
                    } else {
                        velocity = 0;
                        tmc2209_get_velocity(TMC2209_ADDRESS, &velocity);
                        ESP_LOGE(TAG, "BLE unable to set to %lu milliHertz (%d), speed"
                                 " is now %d milliHertz!", context->speed_milliHertz, err);
                    }
                    ESP_LOGI(TAG, "BLE command (0x%04x), write: speed %lu milliHertz.",
                             command.uuid, context->speed_milliHertz);
                    break;
                case COMMAND_READ_PLAY:
                    ESP_LOGI(TAG, "BLE command (0x%04x), read: %s.",
                             command.uuid, context->play_not_stop ? "play" : "stop");
                    break;
                case COMMAND_READ_SPEED_MILLIHERTZ:
                    ESP_LOGI(TAG, "BLE command (0x%04x), read: speed %lu milliHertz.",
                             command.uuid, context->speed_milliHertz);
                    break;
                case COMMAND_UNKNOWN:
                    ESP_LOGI(TAG, "BLE command (0x%04x) received unknown operation: %d (0x08x).",
                             command.uuid, command.value, command.value);
                    break;
                case COMMAND_NONE:
                default:
                    break;
             }
        }
        vTaskDelay(pdMS_TO_TICKS(WATCHDOG_FEED_TIME_MS));
    }

    vTaskDelete(NULL);
}

// Read up to four bytes from an mbuf, returning a
// int32_t made from them (with no endian changes,
// so the source must be litte-endian to work correctly).
static uint32_t mbuf_read(const struct os_mbuf *om)
{
    uint32_t value = 0;

    uint16_t len = os_mbuf_len(om);
    uint16_t read_len = sizeof(value);
    if (read_len > len) {
        read_len = len;
    }
    os_mbuf_copydata(om, 0, read_len, &value);
    ESP_LOGI(TAG, "BLE got data buffer length %d byte(s), extracting value %d.",
             len, value);

    return value;
}

// Play/Stop callback
static int plinky_plonky_play_callback(uint16_t conn_handle, uint16_t attr_handle,
                                       struct ble_gatt_access_ctxt *ctxt, void *arg)
{
    plinky_plonky_context_t *context = (plinky_plonky_context_t *) arg;
    int return_code = BLE_ATT_ERR_UNLIKELY;

    switch (ctxt->op) {
        case BLE_GATT_ACCESS_OP_WRITE_CHR:
        {
            // Read the  value
            uint32_t value = mbuf_read(ctxt->om);
            // Queue the command (non-blocking)
            command_t command = {.uuid = PLINKY_PLONKY_PLAY_UUID,
                                 .type = COMMAND_WRITE_PLAY,
                                 .value = value};
            xQueueSendFromISR(context->ble_command_queue, &command, NULL);
            // Send empty success response
            os_mbuf_free_chain(ctxt->om);
            ctxt->om = ble_hs_mbuf_from_flat("", 0);
            return_code = 0;
        }
            break;
        case BLE_GATT_ACCESS_OP_READ_CHR:
        {
            // Queue the command (non-blocking), purely for information
            command_t command = {.uuid = PLINKY_PLONKY_PLAY_UUID,
                                 .type = COMMAND_READ_PLAY,
                                 .value = 0};
            xQueueSendFromISR(context->ble_command_queue, &command, NULL);

            // Send the current setting
            os_mbuf_append(ctxt->om, &context->play_not_stop, sizeof(context->play_not_stop));
            return_code = 0;
        }
            break;
        default:
        {
            // Queue the command (non-blocking), for information
            command_t command = {.uuid = PLINKY_PLONKY_PLAY_UUID,
                                 .type = COMMAND_UNKNOWN,
                                 .value = ctxt->op};
            xQueueSendFromISR(context->ble_command_queue, &command, NULL);
        }
            break;
    }

    return return_code;
}

// Speed callback.
static int plinky_plonky_speed_callback(uint16_t conn_handle, uint16_t attr_handle,
                                        struct ble_gatt_access_ctxt *ctxt, void *arg)
{
    plinky_plonky_context_t *context = (plinky_plonky_context_t *) arg;
    int return_code = BLE_ATT_ERR_UNLIKELY;

    switch (ctxt->op) {
        case BLE_GATT_ACCESS_OP_WRITE_CHR:
        {
            // Read the value
            uint32_t value = mbuf_read(ctxt->om);
            // Queue the command (non-blocking)
            command_t command = {.uuid = PLINKY_PLONKY_SPEED_MILLIHERTZ_UUID,
                                 .type = COMMAND_WRITE_SPEED_MILLIHERTZ,
                                 .value = value};
            xQueueSendFromISR(context->ble_command_queue, &command, NULL);

            // Send empty success response
            os_mbuf_free_chain(ctxt->om);
            ctxt->om = ble_hs_mbuf_from_flat("", 0);
            return_code = 0;
        }
            break;
        case BLE_GATT_ACCESS_OP_READ_CHR:
        {
            // Queue the command (non-blocking), purely for information
            command_t command = {.uuid = PLINKY_PLONKY_SPEED_MILLIHERTZ_UUID,
                                 .type = COMMAND_READ_SPEED_MILLIHERTZ,
                                 .value = 0};
            xQueueSendFromISR(context->ble_command_queue, &command, NULL);

            // Send the current speed value
            uint32_t speed = context->speed_milliHertz;
            os_mbuf_append(ctxt->om, &speed, sizeof(speed));
            return_code = 0;
        }
            break;
        default:
        {
            // Queue the command (non-blocking), for information
            command_t command = {.uuid = PLINKY_PLONKY_SPEED_MILLIHERTZ_UUID,
                                 .type = COMMAND_UNKNOWN,
                                 .value = ctxt->op};
            xQueueSendFromISR(context->ble_command_queue, &command, NULL);
        }
            break;
    }

    return return_code;
}
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
void app_main(void)
{
    plinky_plonky_context_t *context = &g_plinky_plonky_context;

    ESP_LOGI(TAG, "Plinky-plonky app_main start");

    esp_err_t err = init(context);
    if (err == ESP_OK) {
        ESP_LOGI(TAG, "Initialization complete.");

        err = tmc2209_start(TMC2209_ADDRESS, CONFIG_PLINKY_PLONKY_ENABLE_PIN);

        if (err == ESP_OK) {
            ESP_LOGI(TAG, "Setting TMC2209 %d to %d.", TMC2209_ADDRESS,
                     STEPPER_MOTOR_MICROSTEP_RESOLUTION);
            err = tmc2209_set_microstep_resolution(TMC2209_ADDRESS,
                                                   STEPPER_MOTOR_MICROSTEP_RESOLUTION);
            if (err >= 0) {
                ESP_LOGI(TAG, "Microstep resolution is now %d.", err);
                err = ESP_OK;
            }
        }

#if defined CONFIG_PLINKY_PLONKY_DIAG_PIN && (CONFIG_PLINKY_PLONKY_DIAG_PIN >= 0)
        if (err == ESP_OK) {
            tmc2209_set_stallguard(TMC2209_ADDRESS, -1, 0);
        }
#endif

        // Allow us to feed the watchdog
        esp_task_wdt_add(NULL);

        if (err == ESP_OK) {
            ESP_LOGI(TAG, "Setting motor current to %d mA.", STEPPER_MOTOR_ACTIVE_CURRENT_MA);
            err = tmc2209_set_current(TMC2209_ADDRESS, TMC2209_RSENSE_MOHM,
                                      STEPPER_MOTOR_ACTIVE_CURRENT_MA,
                                      STEPPER_MOTOR_HOLD_CURRENT_PERCENT);
            if (err >= 0) {
                ESP_LOGI(TAG, "Current set to %d mA.", err);
                err = ESP_OK;
            }
        }

        if (err == ESP_OK) {
            ESP_LOGI(TAG, "Forcing StealthChop mode to stay on for quietness.");
            err = tmc2209_set_stealth_chop_threshold(TMC2209_ADDRESS, 0);
            if (err < 0) {
                ESP_LOGI(TAG, "Unable to force StealthChop mode on: %d!", err);
            }
        }

        if (err == ESP_OK) {
            ESP_LOGI(TAG, "Waiting for BLE connections/commands.");
            while (context->running) {
                // Let BLE commands do their thing
                vTaskDelay(pdMS_TO_TICKS(1000));
                esp_task_wdt_reset();
            }
            esp_task_wdt_delete(NULL);
        } else {
            ESP_LOGE(TAG, "TMC2209 configuration failed: 0x%04x (\"%s\")!",
                     err, esp_err_to_name(-err));
        }

    } else {
        ESP_LOGE(TAG, "Initialization failed, system cannot continue, will restart soonish.");
        vTaskDelay(pdMS_TO_TICKS(2000));
    }

    // Setting this will cause the tasks to exit
    g_plinky_plonky_context.running = false;

#if defined CONFIG_PLINKY_PLONKY_DIAG_PIN && (CONFIG_PLINKY_PLONKY_DIAG_PIN >= 0)
    tmc2209_deinit_stallguard(CONFIG_PLINKY_PLONKY_DIAG_PIN);
#endif
    if (context->ble_command_queue){
        vQueueDelete(context->ble_command_queue);
    }
    if (context->diag_semaphore) {
        vSemaphoreDelete(context->diag_semaphore);
    }
    nimble_port_stop();
    tmc2209_deinit();
    esp_restart();
}

// End of file

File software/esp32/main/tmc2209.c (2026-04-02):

/*
 * Copyright 2026 Rob Meades
 *
 * Licensed under the Apache License, Version 2.0 (the "License");
 * you may not use this file except in compliance with the License.
 * You may obtain a copy of the License at
 *
 * http://www.apache.org/licenses/LICENSE-2.0
 *
 * Unless required by applicable law or agreed to in writing, software
 * distributed under the License is distributed on an "AS IS" BASIS,
 * WITHOUT WARRANTIES OR CONDITIONS OF ANY KIND, either express or implied.
 * See the License for the specific language governing permissions and
 * limitations under the License.
 */

/** @file
 * @brief Implementation of the TMC2209 stepper motor driver API for the
 * ESP32-based stepper motor driver.  The code here is at least partly
 * inspired by the code here:
 *
 * https://github.com/janelia-arduino/TMC2209
 */

#include <string.h>
#include <inttypes.h>
#include "esp_log.h"
#include "errno.h"
#include "driver/uart.h"
#include "driver/gpio.h"
#include "string.h"

#include "tmc2209.h"

/* ----------------------------------------------------------------
 * COMPILE-TIME MACROS
 * -------------------------------------------------------------- */

// Logging prefix
#define TAG "tmc2209"

// UART buffer size
#define UART_RX_BUFFFER_SIZE 256

// The maximum number of TMC2209's that can be addressed by this API
#define MAX_NUM_TMC2209 4

// The contents of the sync and reserved fields of a datagram
#define DATAGRAM_SYNC_AND_RESERVED 0x05

// From the table in section 14 of the TMC2209 datasheet,
// the number to multiply VACTUAL by to get a step frequency
// in microHertz
#define VACTUAL_TO_MICROHERTZ (715 * 1000 / 256)

// The maximum value of IRUN or IHOLD, which are 5-bit values.
#define IRUN_OR_IHOLD_MAX 31

/* ----------------------------------------------------------------
 * TYPES
 * -------------------------------------------------------------- */

/* ----------------------------------------------------------------
 * VARIABLES
 * -------------------------------------------------------------- */

// The UART we are using, -1 tmc2209_init() has not been called.
static int32_t g_uart = -1;

// The GPIOs that are wired to the enable pins of the TMC2209's;
// may be -1
static gpio_num_t g_pin_motor_enable[MAX_NUM_TMC2209];

// Table of permitted microstep values: order is important, the index
// into the array corresponds to the MRES value in the CHOPCONF
// register i.e. 256 is an MRES value of 0, 1 is an MRES value of 8.
static const int32_t g_microstep_table[] = {256, 128, 64, 32, 16, 8, 4, 2, 1};

// The VACTUAL register is write-only so keep a shadow of
// the speed in milliHertz to pass back to tmc2209_get_velocity().
static int32_t g_speed_milliHertz = 0;

/* ----------------------------------------------------------------
 * STATIC FUNCTIONS
 * -------------------------------------------------------------- */

// Print out a datagram
static void print_datagram(const char *prefix, uint8_t *p, int32_t length)
{
    char buffer[(sizeof(uint64_t) * 2) + 1] = {0};

    for (int32_t x = 0; (x < length) && (x * 2 < sizeof(buffer)); x++) {
        sprintf(&(buffer[x * 2]), "%02x", *(p + x));
    }
    ESP_LOGD(TAG, "%s0x%s (%d byte(s)).", prefix, buffer, length);
}

 // Clean-up on error or completion
static void cleanup()
{
    if (g_uart >= 0) {
        uart_driver_delete((uart_port_t) g_uart);
        g_uart = -1;
    }
    for (size_t x = 0; x < sizeof(g_pin_motor_enable) / sizeof(g_pin_motor_enable[0]); x++) {
        if (g_pin_motor_enable[x] >= 0) {
            gpio_set_level(g_pin_motor_enable[x], 1);
            g_pin_motor_enable[x] = -1;
        }
    }
}

// Return true if this processor is little-endian, i.e. stores
// the least significant byte at the lowest memory address,
// so the value 0x12345678 read back as an array would
// be 0x12345678, as opposed to 0x78563412 for big-endian.
static bool is_little_endian()
{
    int32_t x = 1;

    return (*((char *) (&x)) == 1);
}

// Convert a buffer of data into a uint32_t for transmission.
static uint32_t endian_convert(uint32_t data)
{
    uint32_t output = data;

    // Transmission order is data bytes 3, 2, 1, 0,
    // so big-endian: reverse if we are little-endian
    if (is_little_endian()) {
        output = 0;
        for (uint32_t x = 0; x < sizeof(data); x++) {
            output |= ((uint32_t) *(((uint8_t *) &data) + x)) << (24 - (8 * x));
        }
    }

    return output;
}

// Calculate the CRC on a datagram
static uint8_t calculate_crc(uint8_t *p, size_t length)
{
    uint8_t crc = 0;
    uint8_t byte;

    for (uint8_t x = 0; x < length; x++) {
        byte = *p;
        for (uint8_t y = 0; y < 8; y++) {
            if ((crc >> 7) ^ (byte & 0x01)) {
                crc = (crc << 1) ^ 0x07;
            } else {
                crc = (crc << 1);
            }
            byte = byte >> 1;
        }
        p++;
    }

    return crc;
}
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

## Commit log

2026-03-28 Initial commit of Blender files and README.mds.
    [plinky_plonky.blend, plinky_plonky.stl]
2026-03-29 Initial commit of ESP32 code.
2026-03-31 Updated README.md and add modified wheel to 3D design.
    [plinky_plonky.blend, plinky_plonky.stl]
2026-04-02 Speed was twice as fast as it should be, now corrected.
    [tmc2209.c]
2026-04-02 Update the Android application to match the frequency halving (or was it doubling: anyhow, they line up now) on the ESP32 side. Also deal more elegantly with Android permissions screens.
2026-04-03 One more thing that fell off fixed: app was no longer stopping rotation on switching from Portrait to Landscape.
2026-04-03 Another Android application update: realised, eventually, after much poking around with Gemini, that it really is true that the BLE APIs on an Android phone are single threaded. How can that be!? In 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
    Hereby, v1.1.4.
2026-04-03 README.md updates.
    [plinky_plonky.blend, plinky_plonky.stl]
